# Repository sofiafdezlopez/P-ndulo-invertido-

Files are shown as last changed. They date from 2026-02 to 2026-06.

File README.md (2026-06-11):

# Péndulo invertido

Somos dos alumnos del Grado de Robótica de la Universidad de Santiago de Compostela. En la asignatura de teoria de control se nos ha designado el trabajo de elaborar un robot "péndulo invertido".
El objetivo de este proyecto es que durante la duración de la materia realizaremos la construcción de robot y su control, que se basa en que el robot sea capaz de estabilizarse y mantenerse en una posición vertical.

Para ello hemos organizado todo nuestro trabajo de la siguiente manera:
- `Mecanica/`: Donde se encuentra toda la información sobre la parte mecánica de nuestro robot.
- `Electronica/`: Donde se encuentra toda la información sobre la parte electrica del robot.
- `Software/`: Donde se encuentra toda la información sobre la parte de la programación del robot.
- `README.md`: Fichero explicativo de todo el proyecto.
  
## Procedimiento a seguir

1. __Revisión de proyectos relacionados__ : Realizar una investigación de proyectos existentes para identificar robots similares ya implementados y documentados.
  
2. __Establecer objetivos__ : Debemos tener una idea clara de lo que tenemos que hacer.

3. __Configuración del hardware__ : Escoger los componentes necesarios para la elaboración del robot.

4. __Diseño del chasis__ : Diseñar el chasis ideal que cumpla con las especificaciones.

5. __Comprobación del funcionamiento de los componentes__ : Verificar el funcionamiento de todo el hardware antes del realizar el montaje.

6. __Montaje__ : Orden de montaje del robot.

7. __Implementación del software__ :

8. __Ajuste del PID__ :

## Revisión de proyectos relacionados

En cuanto a la busqueda de proyectos similares hemos encontrado videos donde te muestran el proceso de como construir y programar un robot autobalanceado pero en ningun momento lo documentan de manera que puedas hacerlo sin ver el video.

## Objetivos

- Elegir y adquirir componentes electromecánicos y electronicos.
- Diseñar e imprimir/fabricar el sistema mecánico del péndulo invertido mediante impresión 3D.
- Diseñar e implementar el controlador del péndulo invertido. Diseño de PCB, fabricación y
soldadura de componentes.
- Realizar la implementación del software de control en el microcontrolador ESP32.
- Sintonizar y ajustar el control PID para el péndulo invertido.
- Cumplir las especificaciones.

### Especificaciones

- El sistema debe ser capaz de __mantenerse en posición vertical__ con una tolerancia de ±5
- El sistema debe __compensar los empujones externos__ y volver a la posición vertical.
- El sistema debe ser capaz de poder __iniciar su funcionamiento desde cualquier posición__.

## Configuración del Hardware

Dado que el propósito principal del robot es medir el ángulo de inclinación respecto al suelo, la configuración de sus componentes es sencilla. Los elementos necesarios son los siguientes:

- ESP32
- 2 motores DC 
- 1 driver dual TB6612FNG
- Sensor MPU6050
- Bateria/pila 9V

## Diseño del chasis

A lo largo del proyecto, desarrollamos tres diseños del chasis, optimizandolo basándonos en los resultados de las pruebas:

- **Modelo 1 (Prototipo Inicial)**: Diseño sencillo de una sola planta con la PCB en la parte superior y la batería en la inferior. No resultó práctico ni eficiente, ya que no se tuvó en cuenta un espacio para el interruptor de encendido y este quedó colgando.

- **Modelo 2 (Estructura de Doble Planta)**: Rediseñamos el chasis para solucionar la falta de espacio del primer modelo. Elevamos la PCB para ubicar la batería justo debajo e incluimos una pequeña estructura para fijar el interruptor. Sin embargo, durante las pruebas, observamos que el robot funcionaba de manera más estable y eficiente a una menor altura respecto al suelo.

- **Modelo 3 (Diseño Final)**: Se mantiene la estructura del segundo modelo, pero introduce diferentes alturas en los enganches de los motores. Al elevar la posición de los motores, logramos bajar el cuerpo del robot, optimizando su centro de gravedad y mejorando su funcionamiento.

## Comprobación del funcionamiento de los componentes
Antes de realizar las pruebas de movimiento completo, es fundamental verificar de forma aislada que cada componente electrónico funciona correctamente. Seguimos esta guía de pruebas:

- **1. Test de Alimentación e InterruptorAcción**: Coloca la batería cargada y acciona el interruptor.

   - **Verificación**: Utiliza un polímetro (multímetro) para comprobar que el voltaje en los puntos clave de la PCB sea el correcto y confirma que el LED de estado del microcontrolador se enciende. Si el LED no se ilumina o detectas anomalías en el voltaje, desconecta la alimentación de inmediato para revisar el circuito en busca de cortocircuitos o polaridades invertidas antes de dañar los componentes.
     
- **2. Calibración y Lectura del Sensor de ÁnguloAcción**: Conecta el robot al ordenador mediante el cable USB y carga un script básico de prueba para el sensor.

   - **Verificación**: Abre el serial monitor. Al mover el robot hacia adelante y hacia atrás, los valores del ángulo respecto al suelo deben variar de forma coherente.
     
- **3. Test de Giro de los MotoresAcción**: Eleva el robot (para que las ruedas no toquen el suelo) y ejecuta un código de prueba que haga girar los motores hacia adelante durante 2 segundos y hacia atrás otros 2 segundos.

   - **Verificación**: Asegúrate de que ambas ruedas giran en el sentido correcto. Si una rueda gira al revés, invierte la polaridad de sus cables en la PCB.
  
## Montaje

**Requisito previo**: La pieza o piezas que componen el chasis deben estar completamente impresas.Para este proyecto, la estructura se imprimió con una BAMBU LAB P1S de la universidad bajo las siguientes especificaciones:

- Material: PLA

- Configuración: Parámetros predeterminados por la universidad.

- Tiempo estimado de impresión: 2 horas y 20 minutos aprox.

Una vez retiradas las piezas de la base de impresión y limpios los soportes, se puede realizar el montaje.

**1. Materiales y Herramientas Necesarias**

Tornillos y tuercas: Especificadas en el apartado de mecánica.

Herramientas: Se necesita soldador de estaño, destornillador de estrella y bridas.

**2. Guía de Ensamblaje Paso a Paso**

Paso 1 -> El sistema de tracción: Se fijan los motores al chasis a la altura deseada.

Paso 2 -> Planta Inferior (Alimentación): Se coloca la pila/bateria en su enganche, implementado en el diseño del chasis.

Paso 3 -> Planta Superior (PCB): Se atornilla la PCB, en nuestro caso la enganchamos con bridas debido a que los agujeros de esta son muy pequeños, y se encaja el interruptor.

## Implementación del Software
El software del robot está desarrollado en C++ sobre Arduino. Se organiza en tres capas: utilidades de test y calibración, una biblioteca de control PID propia, y el programa principal de autobalanceo.

El núcleo del sistema es la biblioteca PIDControl, desarrollada para este proyecto. Encapsula tres variantes de controlador PID que pueden seleccionarse en tiempo de ejecución mediante comandos por puerto serie:

**MODE_STANDARD** – PID clásico posicional con acumulador integral y derivada por diferencias finitas.

**MODE_DISCRETE**– Forma recurrente discreta que opera directamente sobre los tres últimos errores mediante coeficientes A0/A1/A2.

**MODE_FILTERED** – PI incremental combinado con derivada filtrada por transformada bilineal, que atenúa el ruido de alta frecuencia en la señal de error.

La estimación del ángulo de inclinación se obtiene del sensor MPU6050 (acelerómetro + giroscopio) mediante un filtro complementario (α = 0,98), que combina la integración del giroscopio a corto plazo con la referencia del acelerómetro a largo plazo.

Los motores se controlan a través de un driver TB6612FNG, con PWM limitado a 170 cuentas para respetar el voltaje nominal de 6 V con la batería de 9 V. El sistema detecta una caída si el ángulo supera ±24° y detiene los motores automáticamente.

Para más detalles sobre la arquitectura, los algoritmos y la guía de uso, ver `Software/README.md/`.

## Ajuste del PID
El ajuste se realizó de forma manual sobre el robot físico, siguiendo este orden:

- Con Ki=0 y Kd=0, se sube Kp hasta que el robot resiste la caída sin oscilar de forma incontrolable.

- Se incrementa Kd hasta amortiguar las oscilaciones y conseguir un comportamiento casi estable.

- Con Kp y Kd fijados, se añade un Ki pequeño para eliminar el error estacionario. Un valor excesivo desestabiliza el sistema.

- El ángulo de equilibrio real del robot se midió en aproximadamente 6° (el signo depende de la orientación del MPU6050). Los valores que produjeron un balanceo estable fueron:

| Kp | Ki | Kd | dt |
| :---: | :---: | :---: | :---: |
| `17` | `0` | `1.2` | `10 ms` |

De los tres modos probados, MODE_FILTERED mostró la respuesta más suave, ya que el filtro paso-bajo en la derivada reduce el efecto del ruido del MPU6050 sobre los motores.

## Multimedia

<details>
  <summary>Haz clic aquí para ver las fotos y videos</summary>
  
  ### Fotos del modelo
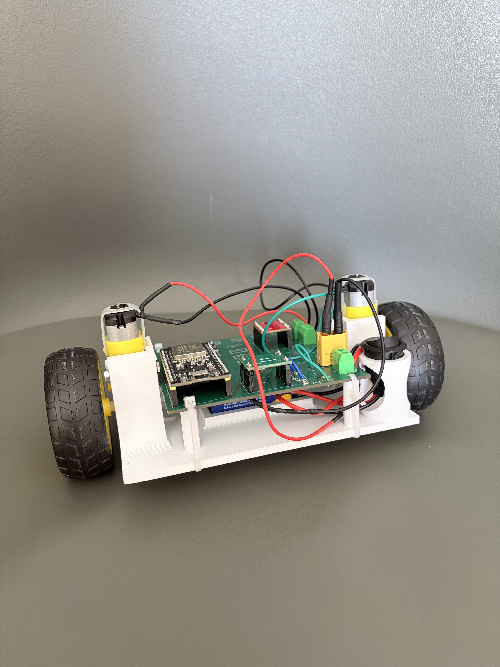
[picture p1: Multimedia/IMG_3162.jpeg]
Vista frontal
  
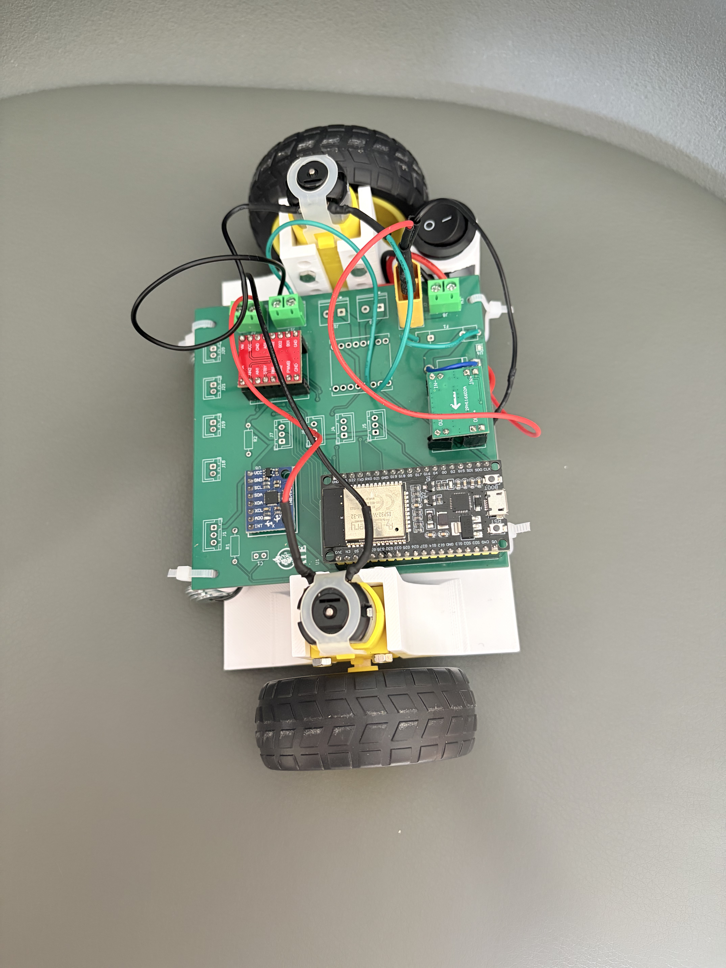
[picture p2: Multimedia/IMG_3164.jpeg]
Vista de planta
  
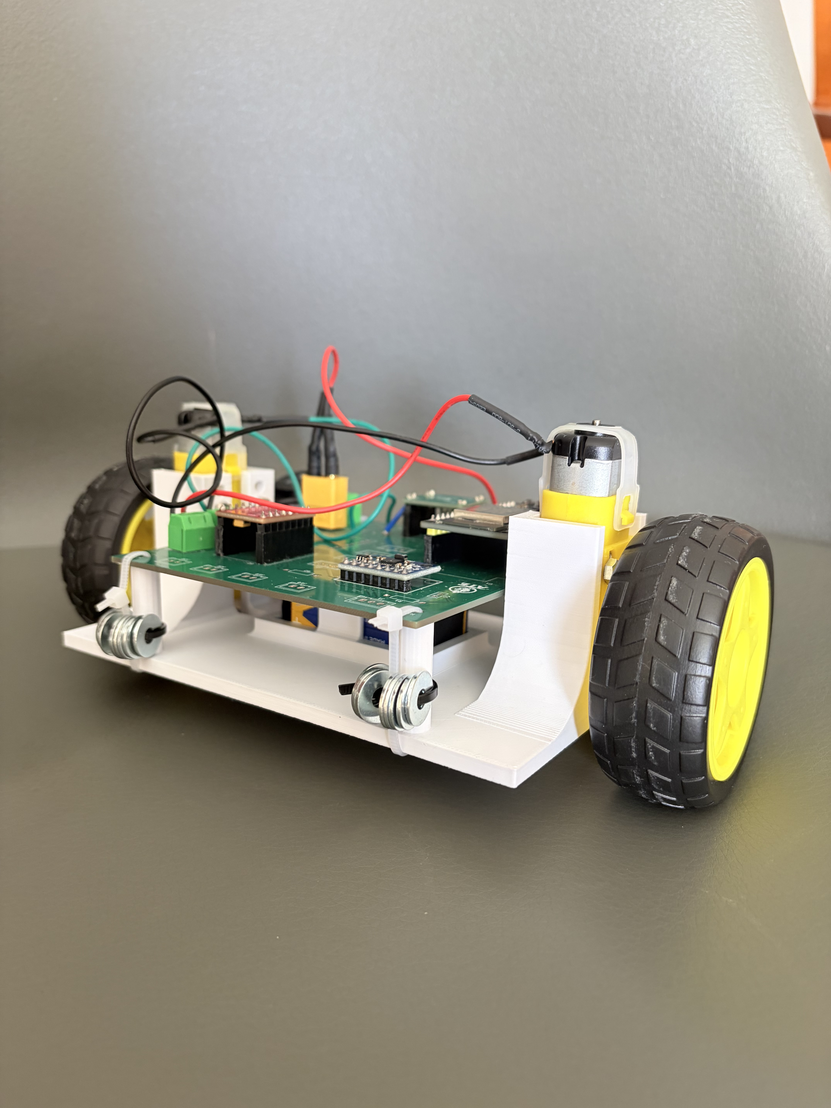
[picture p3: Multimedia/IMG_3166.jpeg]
Vista posterior
  
  
  ### Videos de demostración
  [Mira el video 1 aquí](Multimedia/video1.mov) 
  
  [Mira el video 2 aquí](Multimedia/video2.mov) 
  
  [Mira el video 3 aquí](Multimedia/video3.mov) 
</details>

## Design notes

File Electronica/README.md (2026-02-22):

# Diseño Electrónico del Robot
En esta carpeta se incluyen los diseños y materiales electrónicos necesarios para la construcción de un robot autobalanceado.

La estructura de la carpeta es la siguiente:

- `README.md/`: Este fichero.
- `PCB.zip/`: Carpeta comprimida del modelado de la PCB en Kicad.
- `Componente.md/`: Fichero que contiene la lista de componentes electrónicos.

## Objetivo del Diseño
Placa compacta que aloja:
- Un **ESP32** como MCU/Wi-Fi/Bluetooth.
- Control de **4 motores DC** (2 drivers duales TB6612FNG).
- Lectura de sensores IR y MPU6050.
- Gestión de **alimentación** desde LiPo.
- Conectores para batería, motores, sensores y programación.

## Especificaciones PCB
- **Dimensiones:** ~ 10 × 10 cm 
- **Capas:** 2.

## Adaptaciones de la PCB
La PCB original fue diseñada para su uso en un robot de tipo sumo. Sin embargo, en este proyecto no se utilizarán algunos de los elementos incluidos en el diseño, como por ejemplo los conectores para sensores infrarrojos y finales de carrera, ya que no son necesarios para el funcionamiento del sistema implementado.

Por este motivo, antes del montaje se procederá a eliminar las secciones de la PCB que no serán utilizadas, recortando las partes innecesarias y dejando únicamente la zona correspondiente a los componentes funcionales del proyecto. Esta modificación permite simplificar la estructura del hardware y reducir el tamaño final del módulo electrónico.

## Esquema funcional
- **Entrada batería** → protección (diodo) → **regulador a 5V** → 5V 
- 5V  → ESP32 → **regulador a 3.3V** → 3.3V
- 3.3V: pines GPIO → drivers / sensores / I²C
- **Driver motores (TB6612)**: alimentado a 12V (Vm), señales IN1/IN2 desde ESP32, pin PWM para velocidad.
- Sensores: Conectados a GPIOs del ESP32.

## Protección y seguridad
- Fusible rearmable (PTC) en la entrada de la batería.
- Diodo de protección contra conexión inversa (schottky).
- Indicador LED de encendido (5V) y LED de estado ESP32.

## Prueba de la resistencia de protección en TX0

El uso del GPIO correspondiente a TX0 puede ocasionar problemas. Para mitigar el riesgo de quemar el pin GPIO y las interrupciones en la comunicación serial, así como para facilitar el debug y los tests de forma cómoda y segura, aplicamos las siguientes medidas:

- Colocar una **resistencia en serie** de 4,7KΩ entre el Pin y el Bumper (protección ante el cortocircuito).
- Usa el GPIO TX0 para un bumper (mitigar entradas).

### Procedimiento de prueba

Realiza este procedimiento con el robot APAGADO y desconectado.

1. Pon el multímetro en modo Resistencia (Ω).
2. Coloca una punta en el pin GPIO 1 del ESP32 (o en la soldadura correspondiente).
3. Coloca la otra punta en GND (cualquier punto de masa).
4. **Presiona el Bumper**.
5. **Verifica la lectura:** Debes ver el valor aproximado de tu resistencia (**4.7 kΩ**).

- Si ves **0 Ω** (o muy cerca de cero): La resistencia no está en serie, hay un cortocircuito directo. **No lo enciendas hasta solucionarlo**.
- Si OL (Over Limit): El interruptor no está cerrando el circuito.

### ¿Por qué funciona esto?

Esta configuración es segura y funcional por dos razones matemáticas:

1. **Seguridad (Protección del Pin):**
Si el pin TX0 intenta enviar datos (3.3V) mientras pulsas el botón, la resistencia limita la corriente máxima, evitando quemar el transistor interno del ESP32.

$$I_{max} = \frac{3.3V}{4700\Omega} \approx 0.7 mA$$

*(El ESP32 soporta hasta 12mA, por lo que 0.7mA es totalmente seguro).*

2. **Funcionalidad (Lectura correcta):**
Al leer el botón, el ESP32 activa una resistencia interna de pull-up (~45kΩ). Al pulsar, se crea un divisor de tensión:

$$V_{pin} = 3.3V \times \frac{4.7k\Omega}{4.7k\Omega + 45k\Omega} \approx 0.31V$$

*(0.31V es interpretado como un "LOW" lógico por el ESP32, por lo que detecta la pulsación correctamente).*

Entoces:

- Sin presionar: El pin está en HIGH (3.3V) gracias al pull-up interno. digitalRead devuelve 1.
- Presionado: El pin baja a 0.31V (LOW). digitalRead devuelve 0.

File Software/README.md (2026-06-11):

## Diseño del Software del Robot

En esta carpeta se incluye la implementación del diseño del software necesario para el autobalanceado del robot.

La estructura de la carpeta es la siguiente:
- `README.md/`: Este fichero.

La estructura de este fichero es la siguiente:

1. [Estructura](#estructura)
2. [Diagrama de bloques](#diagrama-de-bloques)
3. [Compilación](#compilación)
4. [Arquitectura](#arquitectura)

## Estructura
``` none
Software/
├── lib/
│   └── PIDControl/              ← Biblioteca de control PID propia
│       ├── src/
│       │   ├── PIDControl.h     ← Declaración de la clase y enumeración PIDMode
│       │   └── ControlPID.cpp   ← Implementación de los tres modos
│       ├── library.properties   ← Metadatos para el IDE de Arduino
│       └── KEYWORDS.txt         ← Coloreado de sintaxis
├── src/
│   ├── main/
│   │   └── main.ino             ← Programa inicial
│   └── main_lib_pid/
│       └── main_lib_pid.ino     ← Programa principal con los tres modos PID
└── test/
    ├── calibracion_mpu6050/
    │   └── calibracion_mpu6050.ino  ← Utilidad de calibración del IMU
    ├── motores/
    │   └── motores.ino              ← Test de giro y dirección de motores
    └── mpu6050/
        └── mpu6050.ino              ← Test de lectura raw del sensor
```

## Diagrama de bloques
``` none
┌─────────────────────────────────────────────────────────┐
│                        ESP32                            │
│                                                         │
│  ┌──────────┐    ┌──────────────┐    ┌───────────────┐  │
│  │ MPU6050  │───▶│   Filtro     │───▶│  Controlador │  │
│  │ IMU I²C  │    │complementario│    │  PID (modo    │  │
│  └──────────┘    └──────────────┘    │  seleccionado)│  │
│                       α=0,98         └──────┬────────┘  │
│                                             │           │
│  ┌──────────────────────────┐               ▼           │
│  │   Serial (115200 baud)   │    ┌──────────────────┐   │
│  │  S → MODE_STANDARD       │    │  Driver TB6612   │   │
│  │  D → MODE_DISCRETE       │    │  Motor A  Motor B│   │
│  │  F → MODE_FILTERED       │    └──────────────────┘   │
│  └──────────────────────────┘                           │
└─────────────────────────────────────────────────────────┘
```

## Compilación

Instalar la biblioteca PIDControl: en el Arduino IDE, Sketch → Include Library → Add .ZIP Library... y seleccionar la carpeta `lib/PIDControl/`.

1- Abrir `src/main_lib_pid/main_lib_pid.ino`.

2- Seleccionar la placa ESP32 Dev Module y el puerto correspondiente.

3- Compilar y subir.

4- Abrir el Monitor Serie a 115200 baud para ver telemetría y enviar comandos.

Para calibrar el MPU6050 (solo necesario si se cambia el sensor o el montaje): abrir y ejecutar `test/calibracion_mpu6050/calibracion_mpu6050.ino` y copiar los offsets resultantes en el sketch principal.

## Arquitectura

**Estimación del ángulo — Filtro complementario**

- El ángulo de inclinación se estima fusionando dos fuentes del MPU6050:
    
   * Acelerómetro: proporciona el ángulo absoluto mediante atan2, pero es ruidoso ante vibraciones.
   * Giroscopio: integra la velocidad angular para obtener el ángulo incremental; preciso a corto plazo pero deriva con el tiempo.
    
- El filtro complementario combina ambas fuentes:
```none
ang_y = α · (ang_y_prev + gy_dps · dt) + (1 − α) · accel_ang
```
&nbsp;&nbsp;&nbsp;&nbsp;&nbsp;&nbsp;Con α = 0,98: el 98 % del peso recae en el giroscopio (respuesta rápida) y el 2 % en el acelerómetro (corrección de deriva).

**Biblioteca PIDControl — Tres modos de control**

- La clase PIDControl implementa tres variantes del controlador PID discreto:

&nbsp;&nbsp;&nbsp;&nbsp;&nbsp;&nbsp;`MODE_STANDARD — PID clásico posicional`

&nbsp;&nbsp;&nbsp;&nbsp;&nbsp;&nbsp;&nbsp;Calcula la salida acumulando la integral del error y la derivada por diferencias finitas:
```none
u(k) = Kp·e(k) + Ki·Σe·dt + Kd·(e(k) − e(k−1))/dt
```
<br>

&nbsp;&nbsp;&nbsp;&nbsp;&nbsp;&nbsp;`MODE_DISCRETE — Forma recurrente directa`

&nbsp;&nbsp;&nbsp;&nbsp;&nbsp;&nbsp;&nbsp;Expresa la salida directamente en función de los tres últimos errores, sin estado acumulado:
```none
u(k) = A0·e(k) + A1·e(k−1) + A2·e(k−2)
```
&nbsp;&nbsp;&nbsp;&nbsp;&nbsp;&nbsp;&nbsp;donde 
```none
A0 = Kp + Ki·dt + Kd/dt, A1 = −Kp − 2·Kd/dt, A2 = Kd/dt.
```

&nbsp;&nbsp;&nbsp;&nbsp;&nbsp;&nbsp;`MODE_FILTERED — PI incremental con derivada filtrada`

&nbsp;&nbsp;&nbsp;&nbsp;&nbsp;&nbsp;&nbsp;Suma incrementalmente la parte PI y aplica un filtro paso-bajo bilineal sobre la parte derivativa para atenuar el ruido:
```none
Δu_PI(k) = (Kp + Ki·dt)·e(k) − Kp·e(k−1)
d(k)      = A0d·e(k) + A1d·e(k−1) + A2d·e(k−2)
fd(k)     = α1·(d(k) + d(k−1)) − α2·fd(k−1)    ← filtro bilineal
u(k)      = u(k−1) + Δu_PI(k) + fd(k)
```
&nbsp;&nbsp;&nbsp;&nbsp;&nbsp;&nbsp;&nbsp;La constante de tiempo del filtro es τ = Kd/(Kp·N), con N = 5 por defecto.

**Control de motores**

- La salida del controlador PID se aplica a ambos motores en sentido opuesto (el robot avanza para compensar la inclinación). La función moveMotor gestiona la dirección mediante los pines IN1/IN2 del driver y la velocidad mediante PWM:

    * Salida positiva → motor A avanza, motor B retrocede.
    * Salida negativa → motor A retrocede, motor B avanza.

- PWM limitado a 170 cuentas (≈ 6,7 V efectivos sobre 9 V de batería).

**Protección por caída**

- Si el ángulo de inclinación supera ±24°, el sistema detiene los motores, reinicia todos los controladores PID y espera a que el robot sea recolocado manualmente. Esto evita que los motores fuercen contra el suelo y protege el hardware.

**Cambio de modo en tiempo de ejecución**

- Enviando S, D o F por el Monitor Serie se cambia el controlador activo sin necesidad de reiniciar el robot ni recompilar. Al cambiar de modo se reinician todos los controladores para evitar transitorios causados por valores residuales en los buffers de error.

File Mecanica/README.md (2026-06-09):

# Diseño Mecánico del Robot
En esta carpeta se incluyen los diseños y materiales mecánicos necesarios para la construcción de un robot autobalanceado.

La estructura de la carpeta es la siguiente:

- `README.md/`: Este fichero.
- `CHASIS.ipt/`: Modelado 3D del chasis en Inventor.
- `CHASIS_V2.stl/`: Archivo .stl del chasis en Inventor.
- `CHASIS_V2.gcode/`: Archivo .gcode del chasis en Inventor.
- `Componentes_mecanicos.md/`: Fichero que contiene la lista de componentes mecánicos.

## Estructura General
- **Dos ruedas motrices** (una de lado izquierdo y otra del lado derecho) con dos motores DC y reducturas, colocados respectivamente.
- **Chasis plano de dos plantas**:
    - **Inferior**: Bateria y motores.
    - **Superior**: Electrónica y sensor.

 ## Dimensiones Orientativas
- **Largo***~ 15 cm
- **Ancho**~ 10 cm
- **Altura**~ 3 cm
- **Distancia entre Ruedas**~ 15 cm
  
 ## Material Utilizado 
 - **Chasis**: PLA/PETG (Impresión 3D)
 - **Motores:** mini micromotores DC con engranajes de rueda dentada.
 - **Ruedas:** diámetro 6–7 cm, goma antideslizante (Mecanum).
 - **Batería:** Varta (9 V).
 - **Cables**
   
## Esquema simple (vista superior)
<pre>
┌─────────────────────────────────────────┐
│        Placa controladora arriba        │
│                                         │ 
[Rueda L]Motor               Motor[Rueda R]
│                                         │ 
│        Batería en el centro             │
└─────────────────────────────────────────┘
</pre>

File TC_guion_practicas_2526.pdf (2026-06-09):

Teoría de Control

Grado de Robótica

2025 - 2026

## GUIÓN DE PRÁCTICAS

## Índice general

1. Modelado de sistemas electromecánicos | 3
2. PID en tiempo contínuo | 7
3. Compensación Proporcional-Integral-Derivativa | 12
4. PID en tiempo discreto | 14
5. Modelado de sistemas en el espacio de estados | 17
EPSE - Campus Terra (Lugo) | 1 / 63 | e.comesana@usc.es

6. Proyecto péndulo invertido | 22
A. Ejemplo de informe del proyecto péndulo invertido | 24
B. Manual de robot Kobuki/Turtlebot2 | 39
EPSE - Campus Terra (Lugo) | 2 / 63 | e.comesana@usc.es

## Práctica 1. Modelado de sistemas electromecánicos

## 1.1. Resumen repaso de Fundamentos de Automática

A continuación se repasan varios conceptos básicos sobre el uso de Matlab y Simulink ya vistos en la asignatura de Fundamentos de Automática

### 1.1.1. Definición de funciones de transferencia

En Matlab las funciones de transferencia se pueden definir de varias formas. Por ejemplo para la función de transferencia

G(s) = Y (s)
X(s)

=

5s − 3
3s

2 + 5s − 7
1. Mediante cociente de polinomios:

% Comentario
num = [5 -3];
den = [3 5 -7];
2. En función de sus ceros (z), polos (p) y ganancia (g):

z = [5 -2];
p = [2+i 2-i -5];
k = 10;
G = zpk(z,p,k);
3. Mediante el uso de variables simbólicas:

s = tf('s') % s es un objeto transfer function. G = 5*s/(3*s^2 + 7);

Notas de interés:

En https://es.mathworks.com/help/control/ref/tf.html está disponible la documentación de la función tf. (https://es.mathworks.com/help/control/ref/tf.html)

El comando tfdata (https://es.mathworks.com/help/ident/ref/dynamicsystem.tfdata.html) permite obtener el numerador y el denominador de una ft.

El comando zpkdata (https://es.mathworks.com/help/ident/ref/dynamicsystem.zpkdata.html) permite obtener los ceros, polos y ganancia de una ft.

Otras funciones para la extracción de información de un ft se pueden consultar en https: //es.mathworks.com/help/ident/data-extraction.html

El comando residue (https://es.mathworks.com/help/matlab/ref/residue.html) permite calcular la descomposición en fracciones simples de una ft.

### 1.1.2. Interconexión y operaciones con bloques

Las funciones feedback, (https://es.mathworks.com/help/control/ref/lti.feedback.html) series (https://es.mathworks.com/help/control/ref/lti.series.html) y parallel (https://es.mathworks.com/help/control/ref/lti.parallel.html) permiten realizar realizar conexiones entre bloques para su reducción:

EPSE - Campus Terra (Lugo) | 3 / 63 | e.comesana@usc.es

K = tf(10, 1);
G = tf(3, [1 1]);
H = tf(4, [1 5 0]);
fb_1 = feedback(G,H,-1);
olp_1 = series(K, fb_1);
C = feedback(olp_1 , 1, -1);

Más información sobre este tipo de funciones en: https://es.mathworks.com/help/control/model-interconnection.html?s_tid=CRUX_lftnav (https://es.mathworks.com/help/control/model-interconnection.html?s_tid=CRUX_lftnav)

### 1.1.3. Visualización de la respuesta de un sistema

La función step (https://es.mathworks.com/help/ident/ref/dynamicsystem.step.html) permite analizar la respuesta de un sistema
ante un escalón unitario. La función plot (https://es.mathworks.com/help/matlab/ref/plot.html) permite obtener la representación gráfica de la respuesta

G = tf([1 10], [2 3 10]);
t_sim = 10; # Tiempo de simulacion.
[y t] = step(G, t_sim);
plot(x, y);
grid;
title('Respuesta␣a␣entrada␣escalon␣de␣G'); xlabel('t(s)');
ylabel('y(t)');

Más información relativa a herramientas análisis de repuesta y
visualización en https://es.mathworks.com/help/ident/response-visualization.html

### 1.1.4. Modelado de sistemas con Simulink

Mediante Simulink podemos crear diagramas de bloques de forma gráfica. Para ejecutarlo:

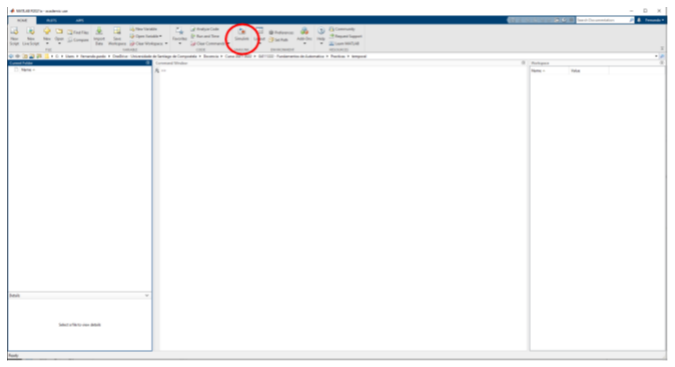
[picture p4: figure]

EPSE - Campus Terra (Lugo) | 4 / 63 | e.comesana@usc.es

Y seleccionar “Create Blank Model”:

Se abrirá el área de trabajo donde construir el modelo de un sistema:

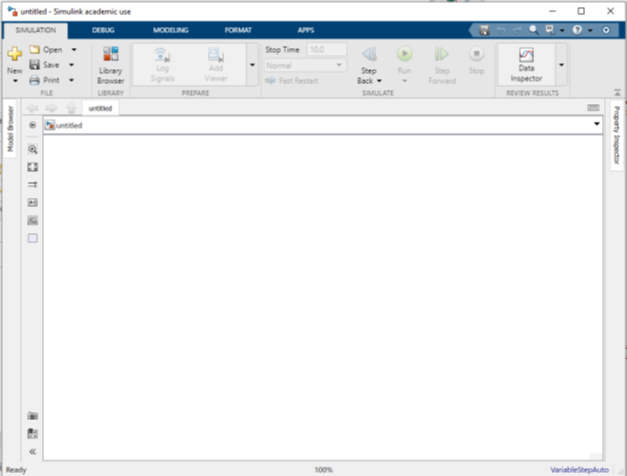
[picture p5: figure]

Para acceder a la librería de componentes pulsar “Library Browser”:

Usaremos las categorías:

Continuous: Análisis de sistemas continuos

Discrete: Análisis de sistemas discretos

Sources: Bloques de generación de señales

EPSE - Campus Terra (Lugo) | 5 / 63 | e.comesana@usc.es

Sinks: Herramientas de visualización

Math operation: Operaciones matemáticas básicas

## 1.2. Ejercicios a realizar

1. Para el sistema de la figura obtener la función de transferencia del sistema X(s)/F(s) y, usando Matlab:
a) Simular la respuesta del sistema ante una entrada escalón.
b) Obtener la respuesta del sistema ante una entrada impulso.
c) Obtener los ceros, polos y ganancia del sistema.
d) Analizar el comportamiento del sistema cuando cambian los valores de las constantes del sistema (m, k y b)
Datos iniciales: m = 2 kg, b = 10 N s m−1

, k = 20 N m−1

2. Para el sistema del problema 1.13 (masa en rotación con acoplamiento elástico), usando Matlab:
a) Simular la respuesta del sistema ante una entrada escalón.
b) Obtener la respuesta del sistema ante una entrada impulso.
c) Obtener los ceros, polos y ganancia del sistema.
d) Analizar el comportamiento del sistema cuando cambian los valores de las constantes del sistema (m, k y b).
3. Construye en Simulink el diagrama de bloques correspondiente al problema 1.9 (suspensión de un coche). Usando los valores disponibles en los apuntes de teoría para este sistema, obtener la respuesta del sistema ante una entrada escalón y una entrada impulso.
4. Construye en Simulink el diagrama de bloques correspondiente al sistema del problema 1.16 (motor con reductora) y obtener la respuesta de sistema ante una entrada escalón. Seleccionar valores para las constantes del sistema y observar el efecto en la respuesta de su cambio.
5. Construye con Simulink el diagrama de bloques del problema 1.19 y responder a las preguntas del problema.
EPSE - Campus Terra (Lugo) | 6 / 63 | e.comesana@usc.es

## Práctica 2. PID en tiempo contínuo

Vamos a trabajar con un sistema realimentado,
el sistema usa la señal de entrada (señal de referencia, r) y la señal de salida (señal manipulada,
y) para generar una señal de error (e) a partir de la cual, por acción del sistema de control (C(s)), generaremos una señal de control (u) para ac-tuar sobre el sistema (F(s)) y llevar la salida del
sistema al valor buscado.

Si recordamos la expresión matemática del PID, el controlador que vamos a usar en esta práctica:

u(t) = Kpe(t) + Ki

∫
e(t)dt + Kd

de(t)
dt

Y en el espacio de Laplace:

U(s) = Kp +

Ki
s

+ Kps

Vemos que para configurar (sintonizar) un controlador PID debemos establecer el valor de tres constantes Kp, Ki y Kd.

## 2.1. PID con Matlab

Para definir un controlador PID en Matlab, podemos construirlo

a partir de su función de transferencia:

Kp = 1;
Ki = 1;
Kd = 1;

s = tf('s');
C = Kp + Ki/s + Kd*s;

o usando la función pid: (https://es.mathworks.com/help/control/ref/pid.html)

Kp = 1;
Ki = 1;
Kd = 1;

C = pdi(Kp, Ki, Kd);
tf(C) % Para mostrar la ft

## 2.2. Ejercicio: Control PID de la fuerza aplicada sobre una masa

Dado el sistema masa-resorte-amortiguador de la figura, la ecuación diferencial que modela el sistema tiene la forma:

m

d

2x
dt²

+ b

dx
dt + kx = F

Que en el dominio de Laplace:

EPSE - Campus Terra (Lugo) | 7 / 63 | e.comesana@usc.es

ms²X(s) + bsX(s) + kX(s) = F(s)

Es decir, que la función de transferencia del sistema es:

X(s)
F(s)

=

1
ms² + bs + k

Si los parámetros del sistema son m = 1 kg, b = 10 N s m−1

, k = 20 N m−1 y la fuerza aplicada es de F = 1 N.

Entonces usando Matlab podemos obtener en primer lugar la respuesta en lazo abierto del sistema con:

s = tf('s');
P = 1/(s^2 + 10*s + 20);
step(P)

Para obtener la respuesta, por ejemplo, a la acción de un controlador proporcional, podemos hacer:

Kp = 300;
C = pid(Kp);
T = feedback(C*P, 1);
t = 0:0.01:2; % Permite definir eje de tiempos con mayor resolucion step(T,t)

### 2.2.1. Cuestiones a resolver

Dado el planteamiento anterior para el sistema mostrado, reponder a las siguientes preguntas:

1. Obtener la respuesta en lazo abierto del sistema ante una entrada escalón unitario. Graficar la entrada y la salida del sistema. ¿De que naturaleza son las magnitudes y cuales son sus unidades de las variables en la gráfica presentada?
2. Testear la respuesta del sistema cuando se emplea un controlador P, PD, PI y PID ¿Qué diferencias se observan entre las respuestas del sistema para cada uno de los controladores? Escoger valores arbitrarios para sintonizar el PID y ajustarlos para entender el efecto que cada termino del PID.
3. Sintonizar un controlador PID de forma manual, intentando obtener el menor tiempo de subida posible sin que se produzca sobreoscilación o sobrepasamiento. El tiempo de subida ha de ser inferior a 0, 1.
4. Desarrollar en Matlab un script que obtenga de forma automática los parámetros de controladores P, PI y PID, empleando el método de Ziegler-Nichols de lazo abierto, descrito en la teoría.
5. Comparar la respuesta entre el sistema controlador por el PID sintonizado manualmente y el sintonizado mediante Ziegler-Nichols
EPSE - Campus Terra (Lugo) | 8 / 63 | e.comesana@usc.es

## 2.3. Sintonizado de PID automático (Autotune)

Matlab ofrece una herramienta automática para escoger el PID accesible a través del comando pid-Tuner. (https://es.mathworks.com/help/control/ref/pidtuner.html) Para obtener el controlador proporcional óptimo (según este autotuner) para el proceso P anteriormente definido

pidTuner(P,'p');

Hacer click en ”Show Parameters”para ver los valores de sintonización del controlador.

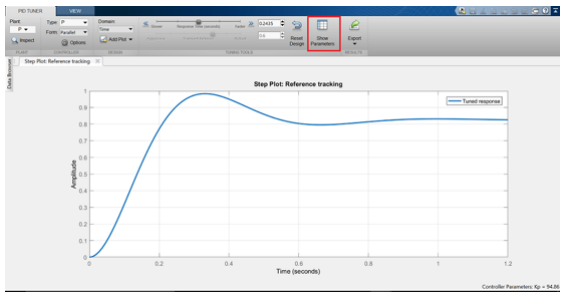
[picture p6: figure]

También podemos realizar la comparación entre un PID base y un PID optimizado, pasando como segundo parámetro a la función pidTuner (https://es.mathworks.com/help/control/ref/pidtuner.html) la función de transferencia de otro PID (baseline).

pidTuner(P,'p');

De nuevo, haciendo clic en ”Show Parameters”se pueden comparar las constantes y características dinámicas del sistema controlado por un PID sintonizado automáticamente y otro previo (baseline).

Por último, mediante los controles disponibles en la herramienta (indicados en la figura anterior), se pueden ajustar los parámetros dinámicos para ajustar la respuesta del sistema.

### 2.3.1. Cuestiones

1. Obtener las respuestas del sistema cuando está controlado con un controlador P, PD, PI y PID sintonizados automáticamente con pidTuner. (https://es.mathworks.com/help/control/ref/pidtuner.html)
2. Comparar las respuestas obtenidas para cada tipo de controlador, ¿que diferencias se observan?
3. Comparar las respuestas obtenidas con los controladores sintonizados con pidTuner (https://es.mathworks.com/help/control/ref/pidtuner.html) y los sintonizados usando el método de Ziegler Nichols.
EPSE - Campus Terra (Lugo) | 9 / 63 | e.comesana@usc.es

4. Comparar el resultado de la sintonización de automática PID para el sistema inicial (función de transferencia P) con el PID sintonizado manualmente para minimizar el tiempo de subida. Usando los controles de pidTuner (https://es.mathworks.com/help/control/ref/pidtuner.html) para ajustar los parámetros dinámicos para igualar

## 2.4. PID con Simulink

Implementar el sistema (servomotor) de la figura, empleando elementos básicos de Simulink. Suponer unos valores arbitrarios para las constantes del PID.

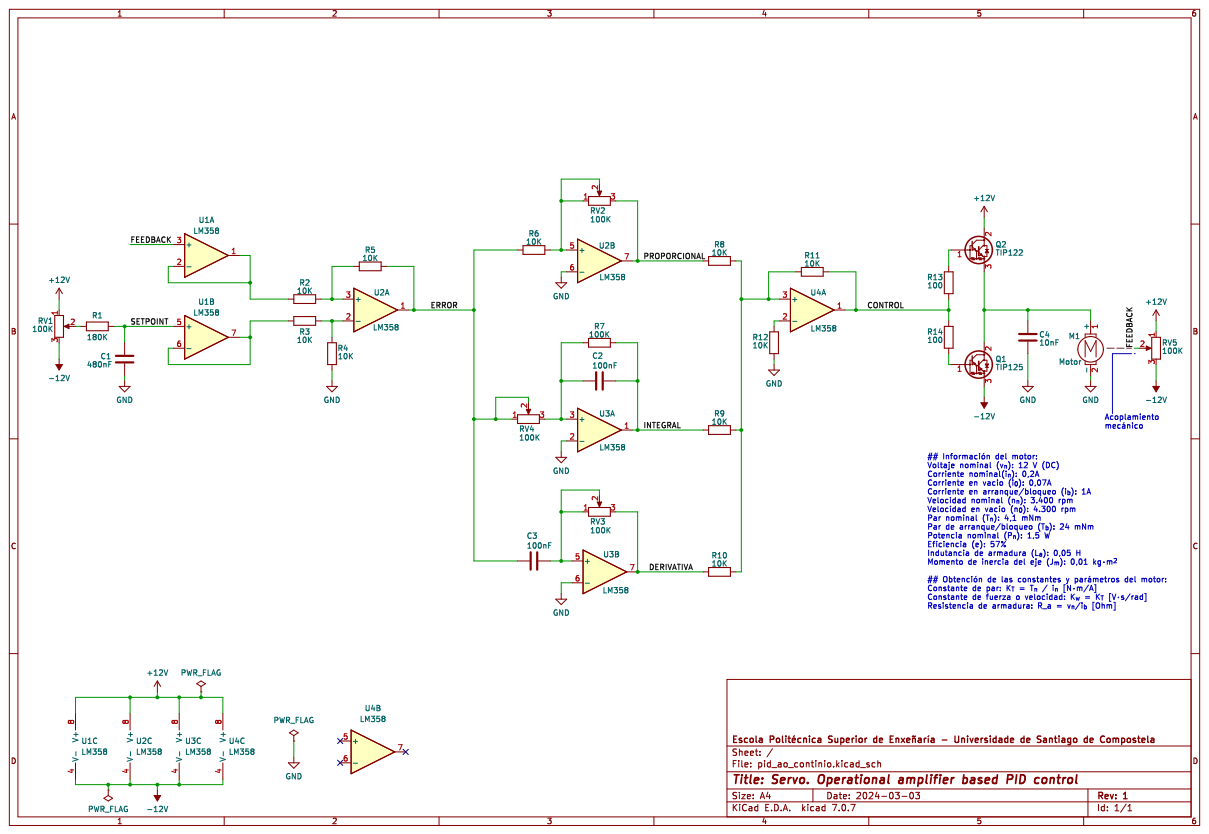
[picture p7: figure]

Sustituir el PID con realizado con amplificadores operacionales con el bloque PID disponible en Simulink

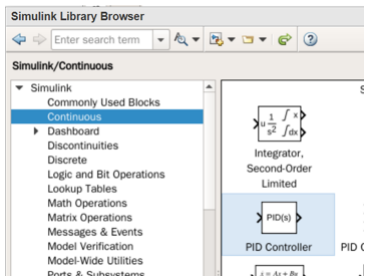
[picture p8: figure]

EPSE - Campus Terra (Lugo) | 10 / 63 | e.comesana@usc.es

El motor empleado tiene las siguientes características:

Parameter | Units | Value | Parameter | Units | Value
Nominal voltaje No-load speed No-load current Rated speed Rated torque Stall torque Starting current | V rpm A rpm mN·m mN·m A | 12 4300 0.07 3400 4.1 24 1.0 | Max power Max efficiency Terminal resistance Terminal inductance Torque constant Speed constant Axis inertia | W % Ω H mN·m/A V·s/rad kg·m² | 1.5 57 12 0.05 20.5 167 0.01

Además tiene acoplado una reductora de relación 48:1 en su eje.

### 2.4.1. Cuestiones

1. Como usarías el método de Ziegler-Nichols para sintonizar las constantes del PID
2. Prueba las herramientas de Autotune de las de dispone el bloque PID de Simulink.
EPSE - Campus Terra (Lugo) | 11 / 63 | e.comesana@usc.es

## Práctica 3. Compensación Proporcional-Integral-Derivativa

La compensación proporcional-integral-derivativa com-bina la acción de la compensación PI y PD:

1. La compensación PD ajusta la respuesta tran-sitoria.
2. La compensación PI mejora el error en estado estacionario.

La función de transferencia de un controlador PID, visto en teoría es:

D(s) = Kp +

Ki
s

+ Kds =

Kds

2 + Kps + Ki
s

Es decir, la función de transferencia del controlador PID tiene dos ceros y un polo en el origen:

La pareja polo/cero cerca del origen se determinan mediante lo visto para el diseño de un compensador PI.

La localización del segundo cero se determina mediante lo visto para el compensador PD.

Procedimiento de diseño de un compensador PID

1. Determinar la posición de los polos dominantes a partir de los requerimientos de diseño para la respuesta en lazo cerrado.
2. Diseñar un compensador PD (posición del cero y ganancia) para colocar el lugar de las raices adecuado y obtener los polos en lazo cerrado buscados.
3. Simular el sistema con el compensador PD e iterar si es necesario para terminar de ajustar la respuesta del sistema.
4. Diseñar el compensador PI y añadirlo al sistema ya compensado con PD, determinar la ganancia necesaria para mantener la localización de los polos dominantes en lazo cerrado buscados.
5. Determinar los parámetros del controlador PID: Kp, Ki y Kd.
6. Simular el sistema PID-compensado e iterar para terminar de ajustar la respuesta.

## 3.1. Ejercicio: Sistema con compensación PID

Diseñar la compensación PID para satisfacer las siguientes especificaciones:

ts = 2s. Considerando un error de 2 %.

%OS = 20 %
Error en estado estacionario cero para una referencia constante.

Para un sistema cuya función de transferencia es:

F(s) = | 15
s

3 + 10s

2 + 27s + 18

EPSE - Campus Terra (Lugo) | 12 / 63 | e.comesana@usc.es

### 3.1.1. Cuestiones

1. Obtener los polos dominantes buscados, en lazo cerrado para las especificaciones listadas anteriormente.
2. Obtener el lugar de las raíces para este sistema en lazo cerrado con un controlador proporcional.
3. Diseñar un compensador PD que satisfaga las condiciones dinámicas:
a) Calcular la contribución angular del cero del compensador PD para que se cumpla el criterio de ángulos.
b) Obtener la posición del cero en el eje real.
c) Obtener el valor de ganancia necesario para conseguir los polos buscado, aplicando el criterio de magnitud.
d) Simular la respuesta del sistema ante una entrada escalón y comparar la respuesta del sistema compensado y sin compensar (con controlador proporcional).
4. Añadir un compensador PI, elegir la posición de su cero y simular e iterar hasta obtener la respuesta buscada.
5. Obtener los valores de las constantes del PID diseñado.
EPSE - Campus Terra (Lugo) | 13 / 63 | e.comesana@usc.es

## Práctica 4. PID en tiempo discreto

El análisis de sistemas de control en tiempo discreto es muy similar al análisis en tiempo continuo. La principal diferencia es que en tiempo discreto, las señales y las funciones de transferencia se representan en el dominio de la frecuencia de la transformada Z en lugar de la transformada de Laplace.

Para realizar el diseño de la implementación de un controlador PID en un microcontrolador (MCU) o una FPGA, se requiere discretizar el controlador PID. La discretización de un controlador PID. Para esto ser realizan aproximaciones para las derivadas de primer orden empleando diferencias finitas.

La señal de salida del controlador y la señal de error se discretizan en el tiempo con un periodo de muestreo ∆t.

## 4.1. Discretización de un controlador PID

La ecuación diferencial de un controlador PID en tiempo continuo es:

u(t) = Kpe(t) + Ki

∫
e(t)dt + Kd

de(t)
dt | (4.1)

y derivando ámbos miembros de la ecuación respecto al tiempo, obtenemos:

du(t)
dt = Kp

de(t)
dt + Kie(t) + Kd

d

2
e(t) dt² | (4.2)

Si la derivada se aproxima como:

f(t)
dt

≈

f(tk) − f(tk−1)
∆t
| (4.3)

siendo k el número de muestra y ∆T el periodo de muestreo.

Entonces la ecuación diferencial del controlador PID se puede aproximar como:

uk − uk−1
∆t

= Kp

ek − ek−1
∆t

+ Kiek + Kd

ek − 2ek−1 + ek−2
∆t

2

(4.4)

que simplificando y agrupando términos tenemos la ecuación para un PID en tiempo discreto:

uk = uk−1 +

(
Kp + Ki∆t +

Kd
∆t

)
ek −

(
Kp +

2Kd
∆t

)
ek−1 +

Kd
∆t
ek−2 | (4.5)

o, en términos de los tiempos de integración y derivación:

uk = uk−1 + Kp

[(1 +
∆t
Ti

+

Td
∆t

)
ek −

(
1 +

2Td
∆t

)
ek−1 +

Td
∆t

ek−2

]
(4.6)

donde Ti = Ki/Kp y Td = Kd/Kp.

EPSE - Campus Terra (Lugo) | 14 / 63 | e.comesana@usc.es

### 4.1.1. Implementación de controlador PID en tiempo discreto

Las ecuaciones anteriores se pueden implementar en un microcontrolador o una FPGA. La implementación mediante un bucle de control que se ejecuta a la frecuencia de muestreo ∆t.

El siguiente pseudocódigo muestra la implementación de un controlador PID en tiempo discreto:

previous_error := 0
integral := 0
start:
error := setpoint - measured_value
integral := integral + error * dt
derivative := (error - previous_error) / dt
output := Kp * error + Ki * integral + Kd * derivative previous_error := error
wait(dt)
goto start

### 4.1.2. PID como un filtro IIR

La transformada Z de un controlador PID en tiempo discreto es:

C(z) = Kp +

Ki∆t
z − 1

+

Kd
∆t

z − 1
z

(4.7)

y expresada en forma de IIR:

C(z) =

(
Kp + Ki∆t +

Kd
∆t

)
+

(
−Kp −

2Kd
∆t

)
z

−1 +

Kd
∆t

z

−2
1 − z

−1

(4.8)

de la cual se puede deducir el bucle de control implementado habitualmente en PLCs y FPGAs.

A0 := Kp + Ki * dt + Kd / dt
A1 := -Kp - 2 * Kd / dt
A2 := Kd / dt
error[2] := 0
error[1] := 0
error[0] := 0
output := u0 // Normalmente el valor inicial del actuador start:
error[2] := error[1]
error[1] := error[0]
error[0] := setpoint - measured_value
output := A0 * error[0] + A1 * error[1] + A2 * error[2] wait(dt)
goto start

### 4.1.3. Filtro pasa baja en el término derivativo

El término derivativo de un controlador PID en tiempo discreto puede causar problemas de ruido en la señal de control, debido a cambios bruscos de la señal de error (flancos de subida o bajada). Para evitar estos problemas, se puede añadir un filtro pasa baja a la acción derivativa de constante de tiempo τ = Td/N, con 3 <= N <= 10, cuya expresión es:

C(z) = 1
τz−1 + 1

(4.9)

EPSE - Campus Terra (Lugo) | 15 / 63 | e.comesana@usc.es

y la ecuación del controlador PID con filtro pasa baja es:

C(z) = Kp +

Ki∆t
z − 1

+

KdTd
∆tN

z

−1

z

−1 + 1

(4.10)

El pseudocódigo que implementa este tipo de controlador PID, con filtro pasa baja, es:

A0 := Kp + Ki*dt
A1 := -Kp
error[2] := 0 // e(t-2)
error[1] := 0 // e(t-1)
error[0] := 0 // e(t)
output := u0 // Normalmente el valor inicial del actuador A0d := Kd/dt
A1d := - 2.0*Kd/dt
A2d := Kd/dt
N := 5
tau := Kd / (Kp*N) // Constante de tiempo del filtro pasa baja alpha := dt / (2*tau)
alpha_1 = alpha / (alpha + 1)
alpha_2 = (alpha - 1) / (alpha + 1)
d0 := 0
d1 := 0
fd0 := 0
fd1 := 0
loop:
error[2] := error[1]
error[1] := error[0]
error[0] := setpoint - measured_value
// PI
output := output + A0 * error[0] + A1 * error[1]
// Filtered D
d1 := d0
d0 := A0d * error[0] + A1d * error[1] + A2d * error[2] fd1 := fd0
fd0 := alpha_1 * (d0 + d1) - alpha_2 * fd1
output := output + fd0
wait(dt)
goto loop

## 4.2. Tareas a realizar

Implementar los tres pseudocódigos anteriores en el microcontrolador ESP32, empleado para la realización del proyecto del péndulo invertido (ver capítulo 6).

Integrar los código realizados en una biblioteca de control PID de vuestra realización. A modo de guía para crear la biblioteca, se puede seguir el tutorial de la realización de una biblioteca en C++ para Arduino en https://www.arduino.cc/en/Hacking/libraryTutorial o de forma más resumida en https://sp.arduino-france.site/crear-libreria/. En el caso de ESP32, se puede seguir el tutorial anterior si se emplea el entorno de desarrollo de Arduino.

Realizar pruebas de funcionamiento de los controladores PID implementados en el péndulo invertido construido.

Publicar el código de las librerías realizadas en el repositorio de GitHub del proyecto del péndulo invertido.

EPSE - Campus Terra (Lugo) | 16 / 63 | e.comesana@usc.es

## Práctica 5. Modelado de sistemas en el espacio de estados

Matlab proporciona un toolbox muy potente (Control System Toolbox). Este toolbox consiste en una colección de funciones que implementan técnicas para el diseño, análisis y modelado de sistemas de control lineales invariantes en el tiempo (LTI: Linear Time-Invariant). Sus características son:

Los sistemas de control pueden modelarse como funciones de transferencia o en el espacio de estados, permitiendo el uso tanto de técnicas de espacio de estados (control moderno) como de funciones de transferencia (control clásico).

Permite trabajar tanto con sistemas continuos como discretos.

Se pueden realizar conversiones entre las distintas representaciones de los sistemas.

Es posible calcular y representar respuestas en el dominio del tiempo, en el dominio de la frecuencia, así como el lugar de las raices.

Dispone de funciones para la asignación de polos, el control óptimo, etc.

Dispone de una interfaz gráfica (LTI Viewer) para el análisis de la respuesta de los sistemas.

## 5.1. Creación del modelo de un sistema continuo en el espacio de estados

Un sistema de control LTI se modela en Matlab como un objeto. Este objeto es una estructura de datos que permite manipular el modelo del sistema como si fuera una única variable Matlab.

Para definir un sistema continuo LTI con la siguiente representación:

¨⃗x(t) = A⃗x(t) + B⃗u(t)

⃗y(t) = C⃗x(t) + D⃗u(t)

podemos usar la función ss (https://es.mathworks.com/help/control/ref/ss.html) es decir, supongamos un sistema, con las siguientes ecuaciones de estado y salida:
[
x¨1(t)
x¨1(t)

]
=

[
0 1

−2 3]
·

[
x1(t)
x1(t)

]
+

[
0
1

]
- u(t)

y(t) = [

6 0]
·

[
x1(t)
x1(t)

]

A = [0 1; -2 3];
B = [0 1]';
C = [6 0];
D = 0;
sys = ss(A, B, C, D)

Esto ha creado un objeto llamado sys, correspondiente al sistema con las ecuaciones mostradas. La variable sys creada es una estructura de datos específica del modelo que permite manipular el sistema como una entidad única. Si quisiéramos extraer los datos asociados modelo, hay dos opciones:

1. Empleando la función ssdata (https://es.mathworks.com/help/ident/ref/dynamicsystem.ssdata.html)

[A, B, C, D] = ssdata(sys)

EPSE - Campus Terra (Lugo) | 17 / 63 | e.comesana@usc.es

2. Accediendo directamente a las propiedades del objeto con el modelo del sistema:

matriz = sys.A;

la variable matriz contiene la matriz de estado del modelo sys.

### 5.1.1. Conversión de modelos entre representación interna y externa

Para convertir un sistema entre distintas representaciones se utilizan las mismas funciones que para crear los modelos. Por ejemplo, para obtener el modelo del sistema en representación externa (función de transferencia) a partir de su modelo en representación interna (ecuanciones de estado), se ejecutaría en Matlab:

systf = tf(sys)

donde sys es el sistema modelado en el espacio de estados y systf el modelo en forma de función de transferencia. Para realizar la operación inversa:

sys = ss(systf)

### 5.1.2. Cálculo y visualización de la respuesta del sistema

El toolbox de control de Matlab también permite obtener la representación gráfica de la salida de un sistema para diferentes tipos de entradas:

Función step: (https://es.mathworks.com/help/control/ref/dynamicsystem.step.html) Respresenta gráficamente la respuesta del sistema ante una entrada escalón unitario, asumiendo que las condiciones iniciales son nulas.

step(sys)

[y, t, x] = step(sys);
% y es la respuesta del sistema
% t vector del tiempo de simulacion
% x evolucion de las variables de estado plot(t, x)

Función initial: (https://es.mathworks.com/help/control/ref/lti.initial.html) Respuesta del sistema ante unas condiciones iniciales determinadas, x0, considerando que la entrada es nula:

initial(sys, x0)
% o
[y, t, x] = initial(sys, x0)

Función lsim: (https://es.mathworks.com/help/control/ref/dynamicsystem.lsim.html) Obtiene la respuesta ante una entrada arbitraria.

lsim(sys, u, t, x0)
% o
[y, ts, x] = lsim(sys, u, t, x0)

donde t es el vector de tiempo de los datos de entrada que se expresan en u. x0 son las condiciones iniciales, si se asumen nulas no es necesario incluirlas.

El toolbox incorpora una interfaz interactiva que facilita el análisis de la respuesta de los modelos LTI, denominada LTI Viewer. Para abrir esta herramienta, ejecutar en Matlab: ltiview (https://es.mathworks.com/help/control/ug/basic-lti-viewer-tasks.html)

La interfaz permite obtener la respuesta de cualquier sistema definido ante diferentes señales de entrada.

EPSE - Campus Terra (Lugo) | 18 / 63 | e.comesana@usc.es

### 5.1.3. Cuestiones

Sea el sistema continuo definido en su representación interna por:

¨⃗x(t) =

0 | 1 | 0
0 | 0 | 1
−50 −20 −10

- · ⃗x(t) +

0
0
1

- · ⃗u(t)

⃗y(t) = [

30 0 0]
- ⃗x(t)

Utilizando las funciones necesarias:

1. Representar el sistema como un objeto LTI.
2. Obtener la respuesta del sistema, la evolución de las variables de estado, considerando una entrada escalón unitario y condiciones iniciales nulas.
3. Obtener la respuesta del sistema y la evolución de las variables de estado, considerando con-diones iniciales x0 = [0, 5, −1] y entrada nula.
4. Obtener la respuesta del sistema y evolución de los estados ante una entrada escalón unitario y condiciones inicales x0 = [0, 5, −1].
5. Obtener la respuesta del sistema cuando la entrada es como la que se muestra en la figura y suponiendo condiciones iniciales nulas

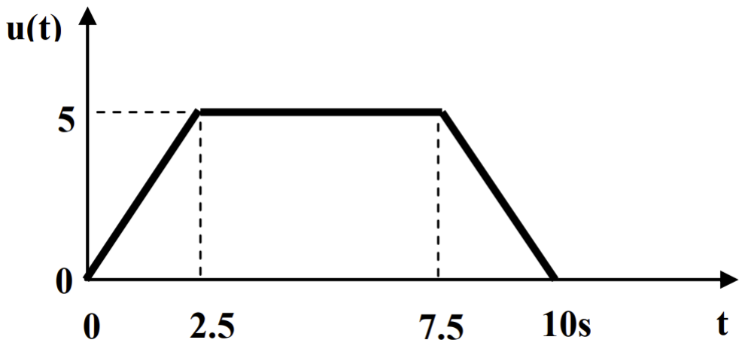
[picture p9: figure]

6. Obtener la función de transferencia del sistema y la salida de dicha función ante un escalón unitario, comprobar que el resultado coincide con la 2ª cuestión.

## 5.2. Controlabilidad y observabilidad de un sistema

En Matlab podemos evaluar la controlabilidad del estado de un sistema usando la función ctrb, (https://es.mathworks.com/help/control/ref/ss.ctrb.html) que devuelve la matriz de controlabilidad del sistema y evaluando su rango con la función rank (https://es.mathworks.com/help/matlab/ref/rank.html) podemos determinar si un sistema es o no controlable.

Del mismo modo con la función obsv (https://es.mathworks.com/help/control/ref/ss.obsv.html) se obtiene la matriz de observabilidad y con ella podremos evaluar si el estado de un sistema es o no observable a partir de un conjunto de salidas.

### 5.2.1. Cuestiones

Usando la descrición del sistema del apartado anterior

1. Obtener la matriz de observabilidad y de controlabilidad del sistema:
EPSE - Campus Terra (Lugo) | 19 / 63 | e.comesana@usc.es

a) Empleando las funciones ctrb (https://es.mathworks.com/help/control/ref/ss.ctrb.html) y obsv. (https://es.mathworks.com/help/control/ref/ss.obsv.html)
b) Realizando el cálculo sin emplear las funciones anteriores, solo operaciones básicas con matrices.

Comprobar que el resultado es el mismo por ambos métodos.

2. Evaluar si el sistema es observable y controlable.

## 5.3. Modelo de estados del robot Turtlebot (opcional)

Un robot con ruedas es aquel que funciona en contacto con el suelo y su movimiento se basa en ruedas accionadas por separado situadas a ambos lados del cuerpo del robot. Así, puede cambiar de dirección variando la velocidad relativa de rotación de sus ruedas. En general, independientemente del número de ruedas que tenga, la velocidad de cada lado tendrá el mismo valor por separado. Por lo tanto, todos los robots con ruedas pueden ser tratados como robots de tracción diferencial con dos ruedas.

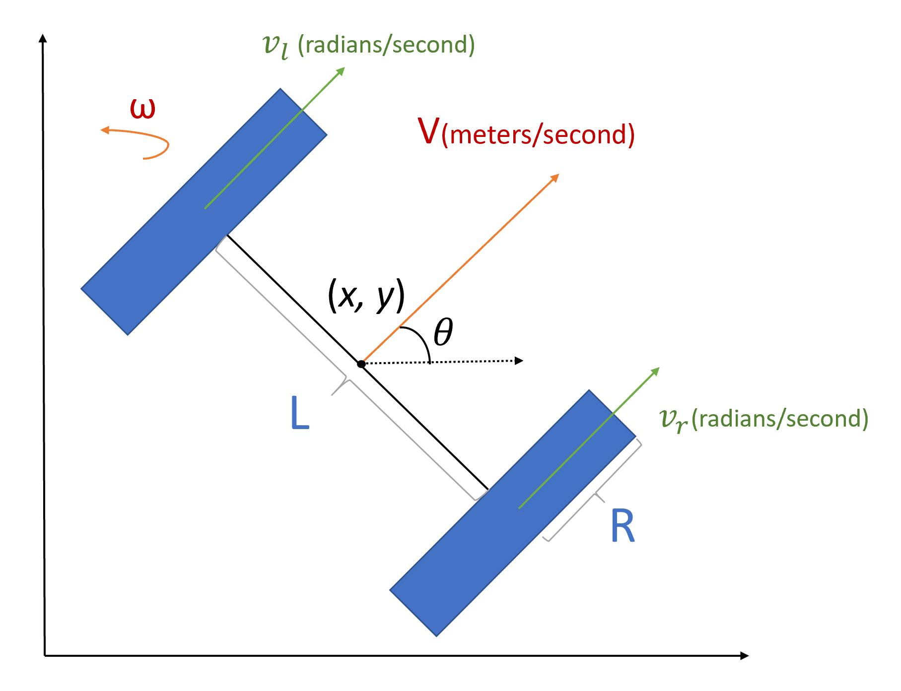
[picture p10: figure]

Si se está diseñando un robot físico y se necesita conocer las verdaderas entradas a las ruedas, es necesario modelar un robot de tracción diferencial. El diferencial de tracción es un sistema de tracción de dos ruedas con actuadores independientes. Normalmente se colocan dos ruedas motrices a cada lado del robot y la dirección hacia el frente se trata como la dirección positiva. Tendrá un estado

EPSE - Campus Terra (Lugo) | 20 / 63 | e.comesana@usc.es

definido por las variables (x, y, θ), que será la posición y dirección del robot en todo instante, y las entradas de este sistema mecánico serán las velocidades de la rueda izquierda (vl) y derecha (vr).

Ref: https://ucr-robotics.readthedocs.io/en/latest/tbot/moRbt.html

## 5.4. Cuestiones

1. Teniendo en cuenta lo anteriormente descrito, plantea un modelo de estados para el movimiento del Turtlebot, usando como variables de entrada y salida las descritas anteriormente. Tener en cuenta que la distancia entre ruedas es L = 23cm y el diametro de las ruedas es de R = 3, 5 cm
2. Teniendo en cuenta la información disponible para las características de los motores que accio-nan las ruedas del Turtlebot, construye un modelo de estados para el sistema electromecánico de accionamiento. Las características del modelo de motor en el Turtlebot, están en “Kobuki User Guide” disponible en el anexo B.
EPSE - Campus Terra (Lugo) | 21 / 63 | e.comesana@usc.es

## Práctica 6. Proyecto péndulo invertido

El objetivo de esta tarea es que durante la duración de la materia realices la construcción de un péndulo invertido y su control. El péndulo invertido es un sistema no lineal, inestable y de doble integración. La inestabilidad del sistema hace que sea un problema interesante para el control, ya que el controlador debe ser capaz de estabilizar el sistema y mantenerlo en una posición vertical.

## 6.1. Objetivos

Elegir y adquirir componentes electromecánicos y electronicos para el proyecto.

Diseñar e imprimir/fabricar el sistema mecánico del péndulo invertido mediante impresión 3D, corte laser u otra técnica adecuada.

Diseñar e implementar el controlador del péndulo invertido. Diseño de PCB, fabricación y soldadura de componentes.

Realizar la implementación del software de control en el microcontrolador ESP32 o Arduino nano.

Sintonizar y ajustar el control PID para el péndulo invertido.

Cumplir las especificaciones a continuación para el sistema completo.

## 6.2. Especificaciones

El sistema debe ser capaz de mantenerse en posición vertical con una tolerancia de ±5

◦

El sistema debe compensar los empujones externos y volver a la posición vertical.

El sistema debe ser capaz de poder iniciar su funcionamiento desde cualquier posición.

## 6.3. Entregables

Repositorio en GitHub con la descripción del sistema, diseño y elementos necesarios para la fabricación de la estructura, diseños y elementos para fabricación de la PCB, implementación del software y sintonización del controlador.

El repositorio debe contener un informe en formato markdown en el fichero README.md del propio repositorio, siguiendo la línea del ejemplo mostrado a continuación.

Demostración del sistema funcionando en una fecha anterior al final de la materia.

## 6.4. Aclaraciones

Para la realización del diseño de partes mecánicas del péndulo invertido, se deberá un de software de diseño 3D “profesional”, como puede ser Fusion 360, FreeCAD, Catia, SolidWorks,

EPSE - Campus Terra (Lugo) | 22 / 63 | e.comesana@usc.es

etc. No se aceptarán diseños realizados en Tinkercad o similares. Se puede acceder a cuentas gratuitas de estudiantes para Fusion 360 (y el resto del software de Autodesk) en https: //www.autodesk.com/education/home, registrándose con el correo de la USC. Todos los proyectos deben incluir algún componente mecánico de diseño y fabricación propia.

Para la fabricación de las piezas mecánicas, se puede usar cualquier técnica de fabricación, como por ejemplo impresión 3D, corte laser, etc. La escuela dispone de un taller de fabricación con impresoras 3D y cortadoras laser y otras herramientas: Laboratorio de Instrumentación. Para poder acceder solicitarlo al profesor de la materia.

Para realizar el diseño de la PCB (esquemático, pcb y ficheros de fabricación) utilizar el software de diseño de PCBs KiCad. (https://www.kicad.org/) No se aceptarán montajes con elementos electrónicos sueltos o montados en protoboard.

Para la fabricación de la PCB, se puede usar cualquier servicio de fabricación de PCBs, como por ejemplo JLCPCB, (https://https://jlcpcb.com/) PCBWay, (https://www.pcbway.com) etc. Existe una web donde se pueden comparar los precios de diferentes fabricantes de PCBs: https://pcbshopper.com/.

## 6.5. Ejemplo de informe

Para que os sirva de guia a la hora de realizar el proyecto y preparar una documentación, os adjunto, en el anexo A, un ejemplo de informe de la realización hecha por Daniel Acevedo de este proyecto de péndulo invertido.

EPSE - Campus Terra (Lugo) | 23 / 63 | e.comesana@usc.es

## Anexo A. Ejemplo de informe del proyecto péndulo invertido

Ejemplo de informe sobre el proyecto/práctica a realizar sobre el péndulo invertido. Este documento debe servir de guía tanto para la realización del proyecto como para la preparación de la documentación a anexar en el repositorio de GitHub del proyecto realizado.

Siendo una guía, se tendrá en cuenta que cada proyecto es diferente y por lo tanto, la documentación a entregar también lo será. Por lo tanto, este ejemplo de informe debe ser tomado como una guía y no como un documento a copiar y entregar.

EPSE - Campus Terra (Lugo) | 24 / 63 | e.comesana@usc.es

### P´endulo Invertido

Daniel Acevedo Facal

14 de diciembre de 2023

### 1. Introducci´on

En este documento se recoge la creaci´on de un primer prototipo de un robot tipo ”p´endulo invertido”.

### 2. Metodolog´ıa seguida

1. Buscar proyectos similares:
Investigar si ya existe un proyecto de un robot similar que est´e funcional y documentado.
2. Investigaci´on general:
Como no existe ning´un proyecto bien hecho y bien documentado, procedemos a investigar c´omo podemos llevar a cabo el proyecto desde cero.
3. Fijaci´on de objetivos:
Es importante tener metas para saber qu´e hardware necesitamos.
4. Selecci´on del Hardware:
Una vez que sabemos qu´e queremos lograr con nuestro robot, tenemos que buscar el hardware con las caracter´ısticas necesarias.
5. Dise˜no del Chasis:
En este apartado debemos resolver dos problem´aticas: tener el peso compensado y tener el centro de gravedad bajo.
6. Prueba de componentes por separado:
Verificamos que todo funcione por separado para luego juntar todo.
7. Montaje: Montamos todos los componentes en el chasis para poder probar el robot al completo.
8. Programaci´on inicial:
Hacemos un primer c´odigo que solo mantenga el robot est´atico en un mismo lugar.
9. Ajuste del PID:
Ajustamos los valores del PID para que el robot se mantenga est´atico.
10. Implementaci´on de control por mando:
Realizamos un c´odigo que nos permita desplazar el robot con un mando Bluetooth.

### 3. Objetivos

1. Estabilidad Perpendicular al Suelo: Garantizar que el robot sea capaz de mantenerse estable en posici´on perpendicular al suelo. Logrado
2. Compensaci´on de Empujones:
Desarrollar la capacidad del robot para compensar empujones y evitar ca´ıdas. Logrado
3. Arranque desde Cualquier Posici´on:
Lograr que el robot pueda iniciar su funcionamiento desde cualquier posici´on inicial. Logrado
4. Reducci´on de Posibilidades de Volcar:
Minimizar las posibilidades de volcamiento y asegurar que el robot no pueda volver a la posici´on incorrecta. Logrado
5. Control mediante Mando Bluetooth:
Implementar un sistema de control que permita manejar el robot a trav´es de un mando Bluetooth.

### 4. Investigaci´on

En relaci´on con la b´usqueda de otros proyectos de este estilo, he detectado una problem´atica: hay varios proyectos hechos con el mismo principio, pero nadie ha creado una documentaci´on del proyecto para ayudar a otras personas que quieran hacerlo. Por lo tanto, tuve que empezar casi desde cero. Aunque hay esta escasez de informaci´on, he podido rescatar algo de informaci´on examinando fotos y v´ıdeos. De ellos, he determinado el hardware que se necesita y el tipo de control para manejar el movimiento (PID).

### 5. Hardware

Para la selecci´on del hardware, se busc´o que el robot se hiciera con elementos b´asicos y comunes para que sea un robot de bajo costo.

1. ESP32:
Para el microcontrolador, he elegido una ESP32, la cual me permitir´a conectar un mando a ella mediante Bluetooth e incluso se podr´ıa usar su conectividad WiFi para diversas funciones. En concreto, se ha utilizado una ESP32-devkitc-v4 que ronda los 5€.

He consultado un par de p´aginas web para informarme al respecto de esta placa, para no alargar este documento dejo los enlaces a continuaci´on: enlace01, enlace02.

2. MPU-6050:
Este sensor tiene incorporado un aceler´ometro y un giroscopio, los cuales vamos a usar para medir la orientaci´on del robot. Las f´ormulas e informaci´on necesaria que he necesitado para usar este sensor est´an en esta p´agina web.
3. TB6612FNG:
El driver que he elegido es una soluci´on m´as moderna que el com´un puente H; su precio es de menos de 2€ y nos permite controlar 2 motores simult´aneamente y de manera independiente. Al igual que con el anterior sensor, la p´agina de la que extraje toda la informaci´on la dejo en el siguiente enlace.
4. Regulador de tensi´on:
Pendiente de documentar lo que se us´o en este aspecto.
5. Bater´ıa:
Primero se realiz´o el robot con un portapilas de 4 pilas AA, pero posteriormente se ha implementado una bater´ıa LiPo que nos proporciona m´as autonom´ıa y facilidad a la hora de recargar el robot.
6. Motores y ruedas:
En este proyecto se han usado los com´unmente usados motores de DC con una reductora, la cual permite un f´acil acople de una rueda que normalmente se vende con el propio motor.

### 6. Chasis

He dise˜nado 4 chasis para el robot, y con el tercero he logrado hacer funcionar el robot. En el desarrollo de estos 3 chasis, he podido valorar cu´ales son los factores determinantes para que el robot funcione.

1. Centro de gravedad:
Es determinante que el centro de gravedad del robot sea el m´as bajo posible. Si el peso est´a muy elevado respecto al suelo, se har´a pr´acticamente imposible que el robot sea capaz de mantenerse derecho.
2. Peso centrado:
Al igual que el centro de gravedad bajo, es decisivo que el peso del robot est´e centrado en el eje de las ruedas, lo que har´a que, combinado con el apartado anterior, el robot deber´ıa mantenerse en la posici´on que queremos sin necesidad de que el robot est´e encendido. Cuanto m´as estable sea el robot gracias al dise˜no del chasis, m´as sencillo nos ser´a ajustar el PID hasta lograr que el robot funcione correctamente.

Ahora voy a explicar los problemas de mis distintos chasis hasta el momento en que fui capaz de hacer que el robot funcionara.

1. Primer chasis:
Este estaba bastante mal hecho, ya que el centro de gravedad estaba demasiado alto, lo que hac´ıa muy complicado que el robot fuese capaz de mantenerse en posici´on vertical.

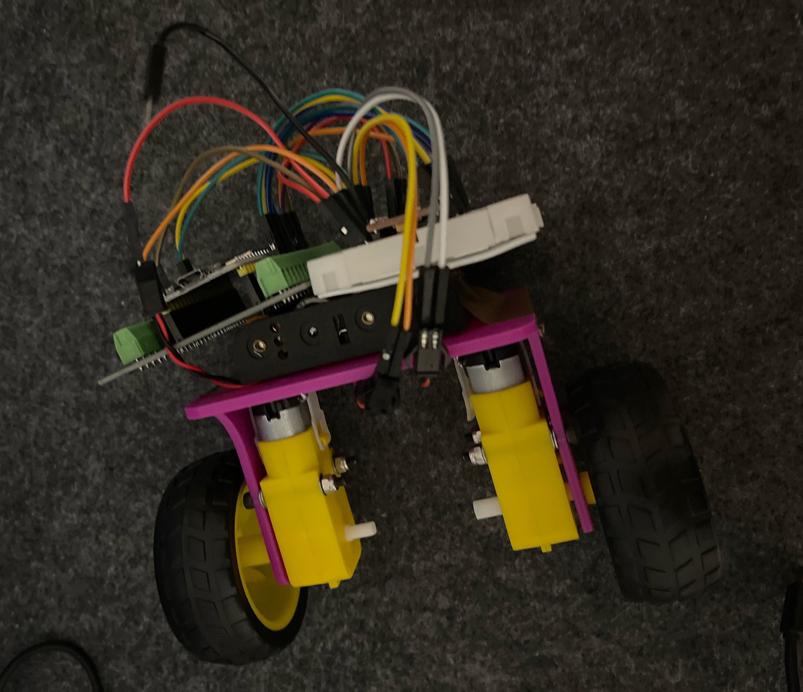
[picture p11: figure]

Figura 1: Chasis01

2. Segundo chasis:
Aunque el centro de gravedad era m´as bajo en este segundo chasis, el problema fue que el peso no estaba centrado, y el robot tend´ıa a inclinarse hacia un lado constantemente.
3. Tercer chasis:
Despu´es de corregir los errores de los dos chasis anteriores, logr´e que el robot funcionara. En este caso, el centro de gravedad estaba muy centrado y a una altura baja, lo que proporcionaba una gran estabilidad incluso cuando el robot estaba apagado.

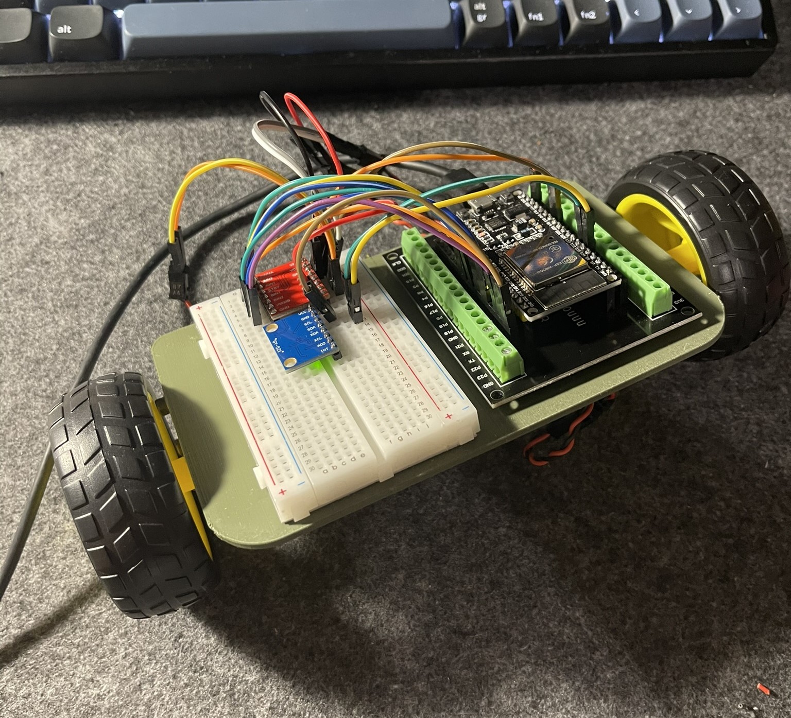
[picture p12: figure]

Figura 2: Chasis03

4. Cuarto chasis:
Este chasis (foto de la portada) me permite incorporar una bater´ıa LiPo sin dejar de tener en cuenta las caracter´ısticas del anterior, que ya funcionaba con pilas.

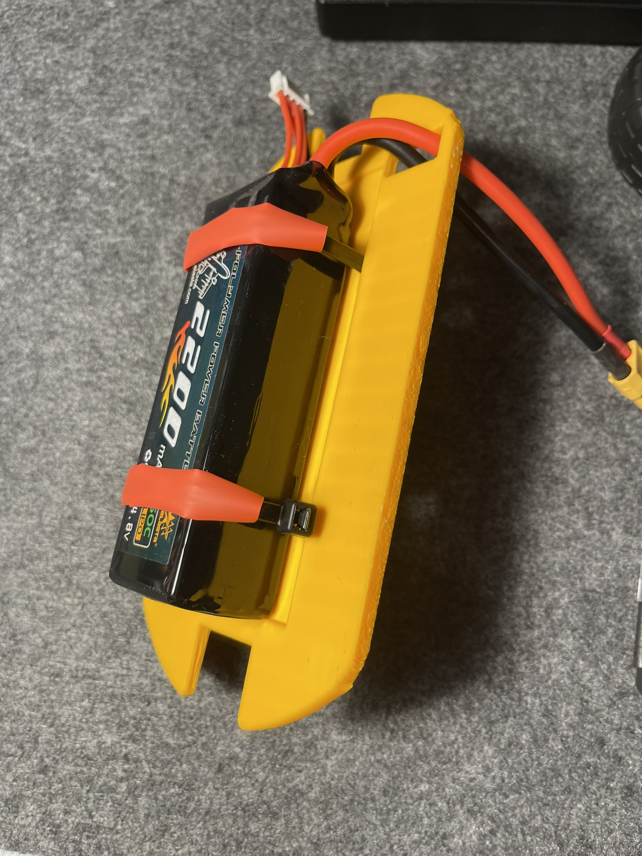
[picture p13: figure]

Figura 3: Chasis04 parte inferior

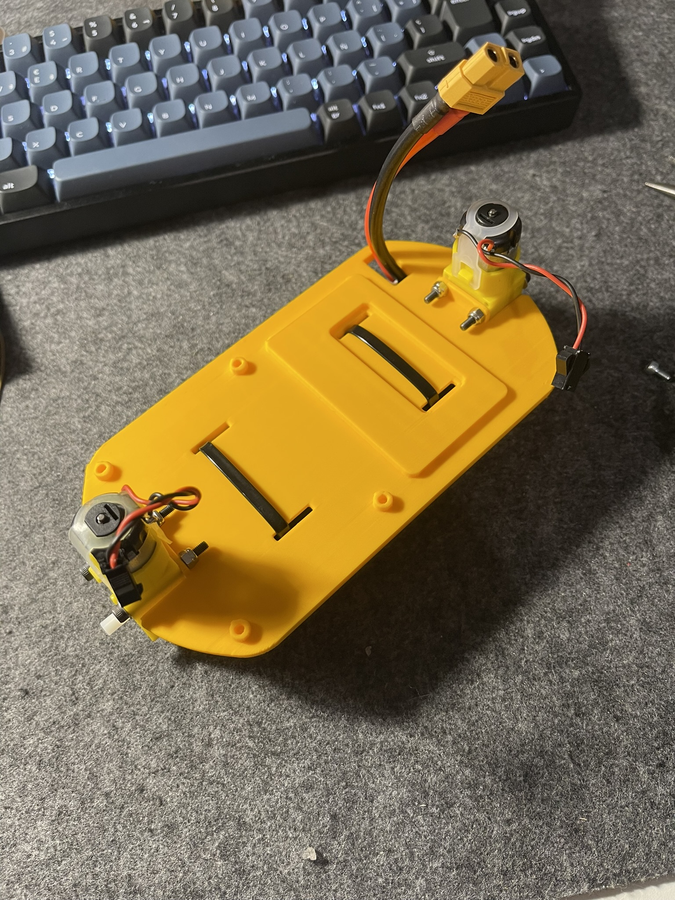
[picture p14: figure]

Figura 4: Chasis04 parte superior

### 7. Prueba de componentes por separado

MPU-6050:
Realizamos una primera prueba para verificar que el sensor funcione.
1 | // Librerias I2C para controlar el mpu6050
2 | // la libreria MPU6050 .h necesita I2Cdev .h, I2Cdev .h necesita Wire .h
3 | # include " I2Cdev .h"
4 | # include " MPU6050 .h"
5 | # include " Wire .h"

6
7 | // La d i r e c c i n del MPU6050 puede ser 0 x68 o 0x69 , dependiendo
8 | // del estado de AD0 . Si no se especifica , 0 x68 e s t a r | implicito
9 | MPU6050 sensor ;

10
11 | // Valores RAW ( sin procesar ) del acelerometro y giroscopio en los ejes x,y,z
12 | int ax , ay , az ;
13 | int gx , gy , gz ;

14
15 | void setup () {
16 | Serial . begin (57600) ; | // Iniciando puerto serial
17 | Wire . begin () ; | // Iniciando I2C
18 | sensor . initialize () ; | // Iniciando el sensor

19
20 | if ( sensor . testConnection () ) Serial . println (" Sensor iniciado correctamente ");
21 | else Serial . println (" Error al iniciar el sensor ");
22 | }

23
24 | void loop () {
25 | // Leer las aceleraciones y velocidades angulares
26 | sensor . getAcceleration (& ax , & ay , & az ) ;
27 | sensor . getRotation (& gx , & gy , & gz );

28
29 | // Mostrar las lecturas separadas por un [tab]
30 | Serial . print ("a[x y z] g[x y z ]:\ t");

31 | Serial . print ( ax ); Serial . print ("\t");
32 | Serial . print ( ay ); Serial . print ("\t");
33 | Serial . print ( az ); Serial . print ("\t");
34 | Serial . print ( gx ); Serial . print ("\t");
35 | Serial . print ( gy ); Serial . print ("\t");
36 | Serial . println ( gz );

37
38 | delay (100) ;
39 | }
Listing 1: C´odigo para probar el MPU6050

Como vemos que el sensor nos proporciona medidas coherentes, procedemos a calibrar el sensor en la posici´on en la que estar´a midiendo.

1 | // Librerias I2C para controlar el mpu6050
2 | // la libreria MPU6050 .h necesita I2Cdev .h, I2Cdev .h necesita Wire .h
3 | # include " I2Cdev .h"
4 | # include " MPU6050 .h"
5 | # include " Wire .h"

6
7 | // La d i r e c c i n del MPU6050 puede ser 0 x68 o 0x69 , dependiendo
8 | // del estado de AD0 . Si no se especifica , 0 x68 e s t a r | implicito
9 | MPU6050 sensor ;

10
11 | // Valores RAW ( sin procesar ) del acelerometro y giroscopio en los ejes x,y,z
12 | int ax , ay , az ;
13 | int gx , gy , gz ;

14
15 | // Variables usadas por el filtro pasa bajos
16 | long f_ax , f_ay , f_az ;
17 | int p_ax , p_ay , p_az ;
18 | long f_gx , f_gy , f_gz ;
19 | int p_gx , p_gy , p_gz ;
20 | int counter =0;

21
22 | // Valor de los offsets
23 | int ax_o , ay_o , az_o ;
24 | int gx_o , gy_o , gz_o ;

25
26 | void setup () {
27 | Serial . begin (57600) ; | // Iniciando puerto serial
28 | Wire . begin () ; | // Iniciando I2C
29 | sensor . initialize () ; | // Iniciando el sensor

30
31 if ( sensor . testConnection () ) Serial . println (" Sensor iniciado correctamente ");

32
33 | // Leer los offset los offsets anteriores
34 | ax_o = sensor . getXAccelOffset () ;
35 | ay_o = sensor . getYAccelOffset () ;
36 | az_o = sensor . getZAccelOffset () ;
37 | gx_o = sensor . getXGyroOffset () ;
38 | gy_o = sensor . getYGyroOffset () ;
39 | gz_o = sensor . getZGyroOffset () ;

40
41 | Serial . println (" Offsets :") ;
42 | Serial . print ( ax_o ); Serial . print ("\t") ;
43 | Serial . print ( ay_o ); Serial . print ("\t") ;
44 | Serial . print ( az_o ); Serial . print ("\t") ;
45 | Serial . print ( gx_o ); Serial . print ("\t") ;
46 | Serial . print ( gy_o ); Serial . print ("\t") ;
47 | Serial . print ( gz_o ); Serial . print ("\t") ;
48 | Serial . println (" nnEnvie cualquier caracter para empezar la calibracionnn ") ;
49 | // Espera un caracter para empezar a calibrar
50 | while ( true ){if ( Serial . available () ) break ;}
51 | Serial . println (" Calibrando , no mover IMU ");

52
53 }

54
55 | void loop () {
56 | // Leer las aceleraciones y velocidades angulares
57 | sensor . getAcceleration (& ax , & ay , & az ) ;

58 sensor . getRotation (& gx , & gy , & gz );

59
60 | // Filtrar las lecturas
61 | f_ax = f_ax -( f_ax > >5) + ax ;
62 | p_ax = f_ax > >5;

63
64 | f_ay = f_ay -( f_ay > >5) + ay ;
65 | p_ay = f_ay > >5;

66
67 | f_az = f_az -( f_az > >5) + az ;
68 | p_az = f_az > >5;

69
70 | f_gx = f_gx -( f_gx > >3) + gx ;
71 | p_gx = f_gx > >3;

72
73 | f_gy = f_gy -( f_gy > >3) + gy ;
74 | p_gy = f_gy > >3;

75
76 | f_gz = f_gz -( f_gz > >3) + gz ;
77 | p_gz = f_gz > >3;

78
79 | // Cada 100 lecturas corregir el offset
80 | if ( counter ==100) {
81 | // Mostrar las lecturas separadas por un [tab]
82 | Serial . print (" promedio :"); Serial . print ("t");
83 | Serial . print ( p_ax ); Serial . print ("\t") ;
84 | Serial . print ( p_ay ); Serial . print ("\t") ;
85 | Serial . print ( p_az ); Serial . print ("\t") ;
86 | Serial . print ( p_gx ); Serial . print ("\t") ;
87 | Serial . print ( p_gy ); Serial . print ("\t") ;
88 | Serial . println ( p_gz );

89
90 | // Calibrar el acelerometro a 1g en el eje z ( ajustar el offset )
91 | if ( p_ax >0) ax_o - -;
92 | else { ax_o ++;}
93 | if ( p_ay >0) ay_o - -;
94 | else { ay_o ++;}
95 | if ( p_az -16384 >0) az_o - -;
96 | else { az_o ++;}

97
98 | sensor . setXAccelOffset ( ax_o );
99 | sensor . setYAccelOffset ( ay_o );
100 | sensor . setZAccelOffset ( az_o );

101
102 | // Calibrar el giroscopio a 0 | /s en todos los ejes ( ajustar el offset )
103 | if ( p_gx >0) gx_o - -;
104 | else { gx_o ++;}
105 | if ( p_gy >0) gy_o - -;
106 | else { gy_o ++;}
107 | if ( p_gz >0) gz_o - -;
108 | else { gz_o ++;}

109
110 | sensor . setXGyroOffset ( gx_o );
111 | sensor . setYGyroOffset ( gy_o );
112 | sensor . setZGyroOffset ( gz_o );

113
114 | counter =0;
115 | }
116 | counter ++;
117 | }
Listing 2: C´odigo para calibrar el MPU6050

Finalmente, probamos el c´odigo que utilizaremos para medir el ´angulo de inclinaci´on del robot.

1 | // Librerias I2C para controlar el mpu6050
2 | // la libreria MPU6050 .h necesita I2Cdev .h, I2Cdev .h necesita Wire .h
3 | # include " I2Cdev .h"
4 | # include " MPU6050 .h"
5 | # include " Wire .h"

6
7 // La d i r e c c i n del MPU6050 puede ser 0 x68 o 0x69 , dependiendo

8 | // del estado de AD0 . Si no se especifica , 0 x68 e s t a r | implicito
9 | MPU6050 sensor ;

10
11 | // Valores RAW ( sin procesar ) del acelerometro y giroscopio en los ejes x,y,z
12 | int ax , ay , az ;
13 | int gx , gy , gz ;
14 | long tiempo_prev ;
15 | float dt ;
16 | float ang_x , ang_y ;
17 | float ang_x_prev , ang_y_prev ;

18
19 | void setup () {
20 | Serial . begin (57600) ; | // Iniciando puerto serial
21 | Wire . begin () ; | | // Iniciando I2C
22 | sensor . initialize () ; | // Iniciando el sensor

23
24 | if ( sensor . testConnection () ) Serial . println (" Sensor iniciado correctamente ");
25 | else Serial . println (" Error al iniciar el sensor ");
26 | }

27
28 | void loop () {
29 | // Leer las aceleraciones y velocidades angulares
30 | sensor . getAcceleration (& ax , & ay , & az ) ;
31 | sensor . getRotation (& gx , & gy , & gz );

32
33 | dt = ( millis () - tiempo_prev ) /1000.0;
34 | tiempo_prev = millis () ;

35
36 | // Calcular los | ngulos | con acelerometro
37 | float accel_ang_x = atan ( ay / sqrt ( pow (ax ,2) + pow ( az ,2) )) *(180.0/3.14) ;
38 | float accel_ang_y = atan (- ax / sqrt ( pow ( ay ,2) + pow (az ,2) )) *(180.0/3.14) ;

39
40 | // Calcular angulo de r o t a c i n con giroscopio y filtro complemento
41 | ang_x = 0.98*( ang_x_prev +( gx /131) * dt ) + 0.02* accel_ang_x ;
42 | ang_y = 0.98*( ang_y_prev +( gy /131) * dt ) + 0.02* accel_ang_y ;

43

44
45 | ang_x_prev = ang_x ;
46 | ang_y_prev = ang_y ;

47
48 // Mostrar los angulos separadas por un [ tab ]

49
50 | Serial . print (" Rotacion en X: | ");
51 | Serial . print ( ang_x );
52 | Serial . print (" tRotacion en Y: ");
53 | Serial . println ( ang_y ) ;

54
55 | delay (10) ;
56 | }
Listing 3: C´odigo completo MPU 6050

Estos c´odigos han sido extra´ıdos de la p´agina web antes citada.

TB6612FNG:
Vamos a probar con un c´odigo b´asico extra´ıdo de la p´agina web citada en la secci´on de hardware. Al igual que los c´odigos del sensor anterior, los he modificado antes de subirlos a la ESP32, ajustando los pines para que sean compatibles con la ESP32.
1 | const int pinPWMA = 6;
2 | const int pinAIN2 = 7;
3 | const int pinAIN1 = 8;
4 | const int pinBIN1 = 9;
5 | const int pinBIN2 = 10;
6 | const int pinPWMB = 11;
7 | const int pinSTBY = 12;
8 | const int waitTime = 2000; | // espera entre fases
9 | const int speed = 200; | // velocidad de giro
10 | const int pinMotorA [3] = { pinPWMA , pinAIN2 , pinAIN1 };
11 | const int pinMotorB [3] = { pinPWMB , pinBIN1 , pinBIN2 };

12

13 | enum moveDirection {
14 | forward ,
15 | backward
16 | };

17
18 | enum turnDirection {
19 | clockwise ,
20 | counterClockwise
21 | };

22
23 | void setup ()
24 | {
25 | pinMode ( pinAIN2 , OUTPUT ) ;
26 | pinMode ( pinAIN1 , OUTPUT ) ;
27 | pinMode ( pinPWMA , OUTPUT ) ;
28 | pinMode ( pinBIN1 , OUTPUT ) ;
29 | pinMode ( pinBIN2 , OUTPUT ) ;
30 | pinMode ( pinPWMB , OUTPUT ) ;
31 | }

32
33 | void loop ()
34 | {
35 | enableMotors () ;
36 | move ( forward , 180) ;
37 | delay ( waitTime );

38
39 | move ( backward , 180) ;
40 | delay ( waitTime );

41
42 | turn ( clockwise , 180) ;
43 | delay ( waitTime );

44
45 | turn ( counterClockwise , 180) ;
46 | delay ( waitTime );

47
48 | fullStop () ;
49 | delay ( waitTime );
50 | }

51
52 | // Funciones que controlan el vehiculo
53 | void move ( int direction , int speed )
54 | {
55 | if ( direction == forward )
56 | {
57 | moveMotorForward ( pinMotorA , speed );
58 | moveMotorForward ( pinMotorB , speed );
59 | }
60 | else
61 | {
62 | moveMotorBackward ( pinMotorA , speed ) ;
63 | moveMotorBackward ( pinMotorB , speed ) ;
64 | }
65 | }

66
67 | void turn ( int direction , int speed )
68 | {
69 | if ( direction == forward )
70 | {
71 | moveMotorForward ( pinMotorA , speed );
72 | moveMotorBackward ( pinMotorB , speed ) ;
73 | }
74 | else
75 | {
76 | moveMotorBackward ( pinMotorA , speed ) ;
77 | moveMotorForward ( pinMotorB , speed );
78 | }
79 | }

80
81 | void fullStop ()
82 | {
83 | disableMotors () ;

84 | stopMotor ( pinMotorA );
85 | stopMotor ( pinMotorB );
86 | }

87
88 | // Funciones que controlan los motores
89 | void moveMotorForward ( const int pinMotor [3] , int speed )
90 | {
91 | digitalWrite ( pinMotor [1] , HIGH );
92 | digitalWrite ( pinMotor [2] , LOW );

93
94 | analogWrite ( pinMotor [0] , speed );
95 | }

96
97 | void moveMotorBackward ( const int pinMotor [3] , int speed )
98 | {
99 | digitalWrite ( pinMotor [1] , LOW );
100 | digitalWrite ( pinMotor [2] , HIGH );

101
102 | analogWrite ( pinMotor [0] , speed );
103 | }

104
105 | void stopMotor ( const int pinMotor [3])
106 | {
107 | digitalWrite ( pinMotor [1] , LOW );
108 | digitalWrite ( pinMotor [2] , LOW );

109
110 | analogWrite ( pinMotor [0] , 0) ;
111 | }

112
113 | void enableMotors ()
114 | {
115 | digitalWrite ( pinSTBY , HIGH );
116 | }

117
118 | void disableMotors ()
119 | {
120 | digitalWrite ( pinSTBY , LOW );
121 | }
Listing 4: C´odigo prueba del driver y motores

### 8. Montaje

El montaje es muy simple; las conexiones de los sensores que debemos realizar est´an explicadas en las p´aginas web mencionadas anteriormente. Adem´as de las conexiones de los sensores, necesitamos alimentar los motores y la ESP32. Ambos trabajan a voltajes distintos, por lo que requerimos dos reguladores de voltaje. Los motores los he alimentado a 9V, y la ESP32-DevKitC-v4 se alimenta a 5V en el pin 5V. Otros modelos se alimentan por el pin VIN a 3.3V, pero en este caso no es as´ı. El esquema el´ectrico bien hecho a´un no est´a listo; lo a˜nadir´e a esta documentaci´on cuando tenga la PCB lista.

### 9. Ajuste del PID

Para poder ajustar el PID, es necesario comprender la funci´on de cada una de las tres componentes de este sistema de control. He consultado esta p´agina para comprender c´omo funciona un PID. La forma de ajustar el PID est´a explicada en esa misma p´agina web, pero en otra secci´on, y la implementaci´on en c´odigo tambi´en se explica en otra secci´on. Cabe destacar que no consult´e esta ´ultima secci´on. Durante el proceso de calibraci´on del robot, he aprendido algunos ”truquitos”´utiles:

Empezar desde 0:
Es crucial comenzar con todos los valores desde 0 y ajustar los valores de manera ordenada e independiente.

Orden de calibraci´on:
Se recomienda iniciar ajustando los valores de Kp hasta lograr que el robot sea capaz de levan-tarse desde el suelo. Una vez logrado esto, se anota el valor que pareci´o ´optimo y se establece la variable a 0.
Luego, se ajusta Kd, buscando un valor en el cual el robot no oscile exageradamente y casi se mantenga en la posici´on deseada.
En el tercer paso, se restablece Kp al valor anotado anteriormente y se deja Kd en el valor ´optimo encontrado. En este punto, Ki a´un se mantiene en 0, pero primero se verifica que el robot casi se mantenga en la posici´on deseada.
Finalmente, se ajusta Ki. Esta componente solo ayuda al robot a alcanzar la posici´on precisa; si las otras dos componentes no se han ajustado correctamente, Ki no cambiar´a radicalmente el comportamiento del robot. En resumen, Kp y Ki son las m´as importantes.

Valores peque˜nos:
Los valores del PID dependen en gran medida de la construcci´on del robot. Es importante tener en cuenta que cuanto mayores sean los valores, m´as agresivo ser´a el movimiento del robot. Se recomienda comenzar con valores menores a 1 y realizar incrementos peque˜nos para evitar que el robot se mueva bruscamente.

### 10. Programaci´on inicial

Al combinar los c´odigos previamente agregados a esta documentaci´on con un control PID, podemos lograr que el robot funcione. Sin embargo, es necesario ajustar los valores del PID para que se adapten a nuestro caso espec´ıfico.

1 | # include " Wire .h"
2 | # include " I2Cdev .h"
3 | # include " MPU6050 .h"

4
5 MPU6050 sensor ;

6
7 | // Definiciones de pines de motores
8 | const int pinPWMA = 16;
9 | const int pinAIN2 = 17;
10 | const int pinAIN1 = 18;
11 | const int pinPWMB = 22;
12 | const int pinBIN1 = 19;
13 | const int pinBIN2 = 21;
14 | const int pinSTBY = 23;

15

16
17 | // Variables del sensor MPU6050
18 | int16_t ax , ay , az ;
19 | int16_t gx , gy , gz ;
20 | long tiempo_prev ;
21 | float dt ;
22 | float ang_x , ang_y ;
23 | float ang_x_prev , ang_y_prev ;

24
25 | // Variables PID
26 | float Kp = 0; // Ajusta estos 3 valores s e g n sea necesario
27 | float Ki = 0;
28 | float Kd = 0;
29 | float integral = 0.0;
30 | float derivative = 0.0;
31 | float previous_error = 0.0;

32
33 | void setup () {
34 | Serial . begin (115200) ;
35 | Wire . begin (32 , 33) ;
36 | sensor . initialize () ;

37
38 | // Configurar pines de motores
39 | pinMode ( pinAIN2 , OUTPUT ) ;
40 | pinMode ( pinAIN1 , OUTPUT ) ;

41 | pinMode ( pinPWMA , OUTPUT ) ;
42 | pinMode ( pinBIN1 , OUTPUT ) ;
43 | pinMode ( pinBIN2 , OUTPUT ) ;
44 | pinMode ( pinPWMB , OUTPUT ) ;
45 | pinMode ( pinSTBY , OUTPUT ) ;
46 | }

47
48 | void loop () {
49 | // Obtener datos del MPU6050
50 | sensor . getAcceleration (& ax , & ay , & az ) ;
51 | sensor . getRotation (& gx , &gy , & gz );

52
53 | // Calcular | ngulos | con el a c e l e r m e t r o
54 | float accel_ang_x = atan ( ay / sqrt ( pow (ax , 2) + pow (az , 2) )) * (180.0 / PI ) ;
55 | float accel_ang_y = atan (- ax / sqrt ( pow ( ay , 2) + pow (az , 2) )) * (180.0 / PI );

56
57 | // Calcular | ngulo | de r o t a c i n con giroscopio y filtro complementario
58 | dt = ( millis () - tiempo_prev ) / 1000.0;
59 | tiempo_prev = millis () ;
60 | ang_x = 0.98 * ( ang_x_prev + ( gx / 131.0) * dt ) + 0.02 * accel_ang_x ;
61 | ang_y = 0.98 * ( ang_y_prev + ( gy / 131.0) * dt ) + 0.02 * accel_ang_y ;

62
63 | ang_x_prev = ang_x ;
64 | ang_y_prev = ang_y ;

65
66 | // Control del p n d u l o invertido usando PID
67 | float desired_angle = 0.0; | // | ngulo | deseado para mantener el equilibrio
68 | float error = desired_angle - ang_x ; | // Calcular error

69
70 | integral += error * dt ;
71 | derivative = ( error - previous_error ) / dt ;

72
73 float motor_speed = Kp * error + Ki * integral + Kd * derivative ;

74
75 | // Controlar los motores
76 | enableMotors () ;
77 | moveMotor ( pinPWMA , pinAIN1 , pinAIN2 , motor_speed );
78 | moveMotor ( pinPWMB , pinBIN1 , pinBIN2 , motor_speed );

79
80 | // Mostrar los | ngulos | y la velocidad de los motores
81 | Serial . print (" Rotacion en X: ") ;
82 | Serial . print ( ang_x );
83 | Serial . print (", Error : ");
84 | Serial . print ( error );
85 | Serial . print (", Velocidad de los motores : ");
86 | Serial . println ( motor_speed );

87
88 | // Actualizar el error anterior
89 | previous_error = error ;

90
91 | delay (1) ; // Reducir el tiempo de espera para aumentar la frecuencia de muestreo
92 | }

93
94 | // Funciones adicionales
95 | void moveMotor ( int pinPWMA , int pinIN1 , int pinIN2 , float speed ) {
96 | if ( speed > 0) {
97 | digitalWrite ( pinIN1 , HIGH );
98 | digitalWrite ( pinIN2 , LOW );
99 | analogWrite ( pinPWMA , speed );
100 | } else {
101 | digitalWrite ( pinIN1 , LOW );
102 | digitalWrite ( pinIN2 , HIGH );
103 | analogWrite ( pinPWMA , - speed );
104 | }
105 | }

106
107 | void enableMotors () {
108 | digitalWrite ( pinSTBY , HIGH );
109 | }
Listing 5: C´odigo inicial completo

### 11. Control con mando

Este apartado a´un est´a por desarrollarse.

## Anexo B. Manual de robot Kobuki/Turtlebot2

Manual de usuario del robot Kobuki/Turtlebot2 para la extracción de parámetros de los motores del robot, para la realización del ejercicio de modelado en el espacio de estados.

EPSE - Campus Terra (Lugo) | 39 / 63 | e.comesana@usc.es

# Kobuki User Guide

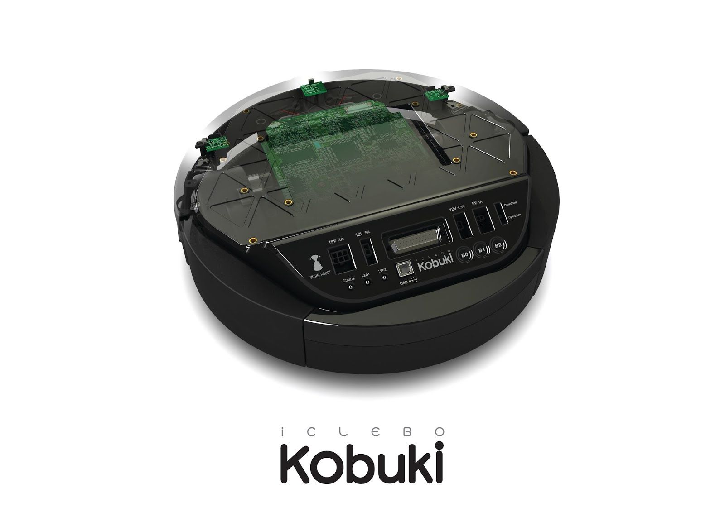
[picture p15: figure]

Version 1.1.0
2017/03/15

## Contents

Contents

About

Basic Usage
Charging
First Run
Software
Problems

Advanced Usage
Replacing Batteries
Updating Firmware
Linux
Windows
Serial Port Connectivity
Adding a Custom Sensor Array

Specifications
Safety Guideline
Functional
Hardware
Software

Anatomy
Top View
Bottom View
Control Panel
Connectors
Models & Drawings
Motors
Gyro
Power Adapter
Batteries
Serial Port

Firmware
Communication
Protocol Specification
Version Checking
Updating
Special Firmware Modes
Activating
Random Walker Mode
Arduino / Embedded Board Support Mode

ChangeLog

License

## About

Introducing Korea’s first robotic turtle.

kobuki [거북이] n. turtle

Kobuki is robotically engineered to be long-lived, tough and fast. With high performance batteries, Kobuki will tirelessly work alongside you through those long coffee-powered nights. He’ll also happily burden himself with your modded array of sensors, actuators, laptops, embedded boards, portside cannons and do it all at a speed that makes his real world cousins seem like … well, turtles.

Use him for serving 치맥 (chi-mek), chasing your neighbour’s kids or simply, to make your own robot ideas become reality.

Kobuki is still young, don’t expect him to remain as he is . Kobuki’s development has already been significantly influenced by the community and as he marches towards old age, we will continue to work with the community and you to ensure he becomes better with time.

Sincerely,
Kobuki Team.

## Basic Usage

Make sure be aware of the safety guidelines.

### Charging

Connect the power adapter to Kobuki or dock Kobuki in the docking station. If Kobuki is turned on, you will hear a short sound when charging starts and the LED will light up appropriately.

- Green : fully charged
- Blinking Green : charging
- Orange : low battery

Tip: the battery still charges if Kobuki is off, but you will not see the LED, nor hear sounds

### First Run

You want to see Kobuki in action without further ado? Kobuki has a special random walker mode embedded into the firmware which you can activate on start-up:

1. Turn on Kobuki.
2. Within the first 3 seconds press the B0 button and hold for 2 seconds.
3. LED2 will start blinking and Kobuki wander around.

Tip: this was introduced to the firmware in v1.1.0. In case your kobuki is not running this or a later version, please refer to the section about updating the firmware.

### Software

In order to gain access to all of Kobuki’ s features, you will need an external computing unit (pc/laptop/tablet/embedded board) with software which communicates with Kobuki. Officially supported systems include:

## Build Your Own Kobuki Driver

Use the Serial Protocol

## Linux C++ Application

Use the Kobuki C++ Driver

## Kobuki for ROS

Use the Kobuki ROS World

Alternatively, you can get started with the Turtlebot 2 Platform which runs on a Kobuki base.

Info: other platforms have had experimental support at one stage or another (windows/arduino/android).

### Problems

Reach out on the following channels:

## Advanced Usage

- Kobuki User’s Mailing List: kobuki-users@yujinrobot.com
- ROS Community Answers: http://answers.ros.org/questions/tags%3Akobuki
- Yujin Sales Support: kobuki@yujinrobot.com

Note: Kobuki comes with a 1 year warranty. In case you bought Kobuki from another one of Yujin Robot’s distributors, please contact them, otherwise email Yujin Sales Support.

### Replacing Batteries

Warning: the electronics does not support the use of multiple battery packs at the same time!

Flip the kobuki | Open the case
Unplug | Swap batteries
Replug | Replace the case

### Updating Firmware

If you have a ROS installation, you can find the current version by running:

$ rosrun kobuki_driver version_info
# Version Info:

* Hardware Version: 1.0.4
* Firmware Version: 1.2.0
* Software Version: 0.7.7
* Unique Device ID: 97713968-842422349-1361404194

Alternatively you can compile version_info.cpp (no ROS) to create your own version checker.

Linux

The Flashing Utility

# Download & build the flashing utility

$ wget http://files.yujinrobot.com/kobuki/firmware/stm32flash-0.4.tar.gz $ tar -xvzf stm32flash.tar.gz
$ cd stm32flash
$ make

Download the Firmware

# choose the firmware version from http://files.yujinrobot.com/kobuki/firmware # e.g. latest

$ wget http://files.yujinrobot.com/kobuki/firmware/kobuki_firmware-latest.hex

Identify the ttyUSBx Port

If you have a udev rule installed, it will show up as /dev/kobuki, but if not, you can typically find it under one of the ttyUSB ports, e.g. /dev/ttyUSB0. If you are not sure, type dmesg into a terminal, unplug and replug the robot and type dmesg again. You should now be able to see which port is assigned to the robot (more precisely the FTDI USB to serial converter).

Switch to Download Mode

1. Connect the robot to your PC using the USB cable
2. Turn off the robot (switch on the side)
3. Switch from normal runtime mode to firmware download mode

This simply changes the type of data that is sent back and forth along the usb connection. You can do this by moving the switch illustrated below into the ‘download’ (up) position. Note that this switch is embedded into the robot cover so it isn’t easily thrown by accident – you may need thin plyers or some similar tool. You can find the mode switch mechanism on the right side of the control panel -see the image below.

Flashing

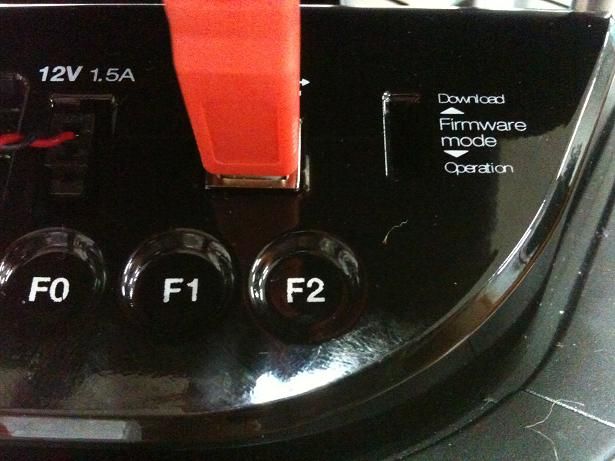
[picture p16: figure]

Note: The following instructions assume flashing of kobuki_firmware-latest.hex and port /dev/ttyUSB0. Modify these if necessary.

Warning: you need to execute the flashing command IMMEDIATELY after turning the robot on!

1. Turn off the robot
2. Check that the switch is in download mode
3. Turn on the robot

$ ./stm32flash -b 115200 -w kobuki_firmware_firmware-latest.hex /dev/ttyUSB0 stm32flash 0.4

http://stm32flash.googlecode.com/

Using Parser : Intel HEX
Interface serial_posix: 115200 8E1
Version | : 0x22
Option 1 | : 0x00
Option 2 | : 0x00
Device ID : 0x0414 (High-density)
- RAM | : 64KiB (512b reserved by bootloader)
- Flash | : 512KiB (sector size: 2x2048)
- Option RAM : 16b
- System RAM : 2KiB
Write to memory
Erasing memory
Wrote address 0x0800a3f0 (100.00%) Done.

Rebooting

- Turn off the robot power
- Flick the firmware switch back to ‘Operation’ mode.
- Turn on the robot power
- I’m happy, you should be too!

Windows

The Flashing Utility

- Download and install the windows flashing utility

Download the Firmware

Find and download the version of the firmware you wish to flash from the Kobuki FW File Server.

Identify the COM Port

Usually if this will show up on COM1, but check to make sure.

Switch to Download Mode

1. Connect the robot to your PC using the USB cable
2. Turn off the robot (switch on the side)
3. Switch from normal runtime mode to firmware download mode

This simply changes the type of data that is sent back and forth along the usb connection. You can do this by moving the switch illustrated below into the ‘download’ (up) position. Note that this switch is embedded into the robot cover so it isn’t easily thrown by accident – you may need thin plyers or some similar tool. You can find the mode switch mechanism on the right side of the control panel -see the image below.

Flashing

1. Turn off the robot
2. Check that the switch is in download mode
3. Turn on the robot

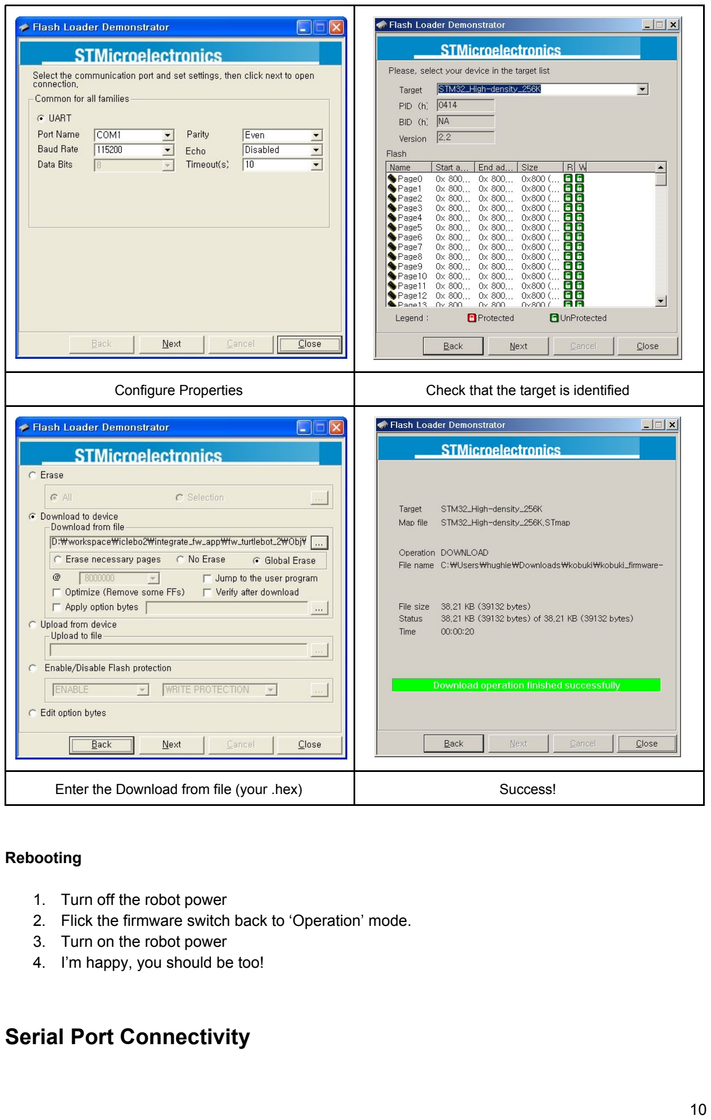
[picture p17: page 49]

Configure Properties | Check that the target is identified
Enter the Download from file (your .hex) | Success!

Rebooting

1. Turn off the robot power
2. Flick the firmware switch back to ‘Operation’ mode.
3. Turn on the robot power
4. I’m happy, you should be too!

### Serial Port Connectivity

Many embedded boards do not have usb interfaces, or the embedded board doesn’t have the necessary ftdi32 serial->usb support. In these cases it is simpler to utilise the serial port on Kobuki’s expansion port to driving kobuki by serial interface instead of USB.

Pinouts

Pictured below are the pinouts of Kobuki’s expansion port, include the serial pins. The minimum number of required pins for serial communication is three; TX, RX, and GND. Additionally EX3.3 or EX5 can be used for powering external devices, such as line transceiver.

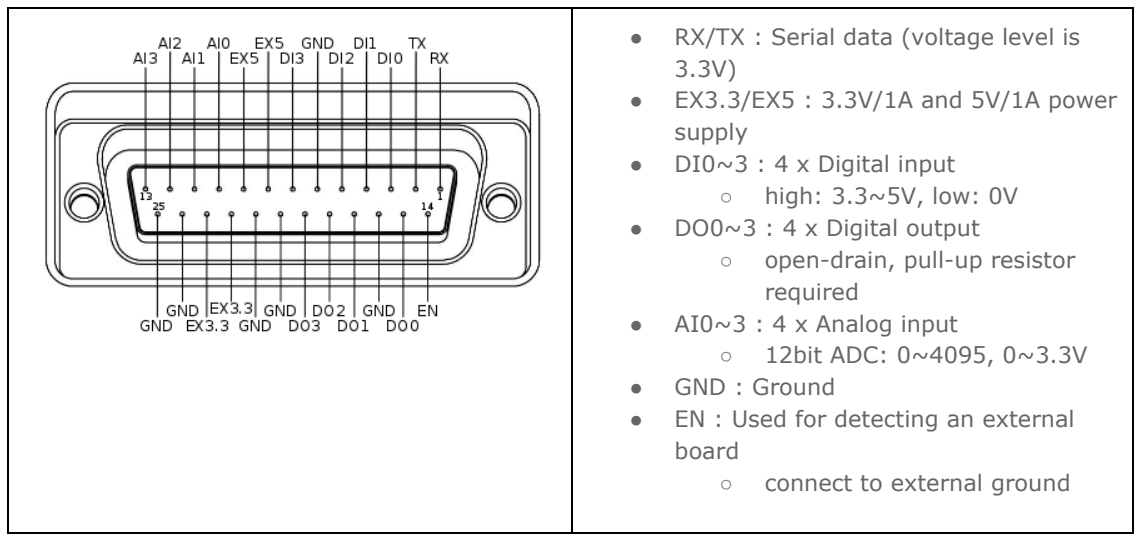
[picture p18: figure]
● RX/TX : Serial data (voltage level is 3.3V) ● EX3.3/EX5 : 3.3V/1A and 5V/1A power supply ● DI0~3 : 4 x Digital input ○ high: 3.3~5V, low: 0V ● DO0~3 : 4 x Digital output ○ open-drain, pull-up resistor required ● AI0~3 : 4 x Analog input ○ 12bit ADC: 0~4095, 0~3.3V ● GND : Ground ● EN : Used for detecting an external board ○ connect to external ground

Connections

a) RS-232 Interface

The voltage level of serial port is 3.3V. To connect kobuki with the standard RS-232 serial port, you should use line transceiver in the middle to convert voltage level. MAX232 chip is typical solution for it. Below diagram show simplified typical example of connections between Kobuki and SBC (your embedded board, laptop or pc). EX3.3 pin is used to powering line transceiver. It can be EV5 pin or external power sources from outside.

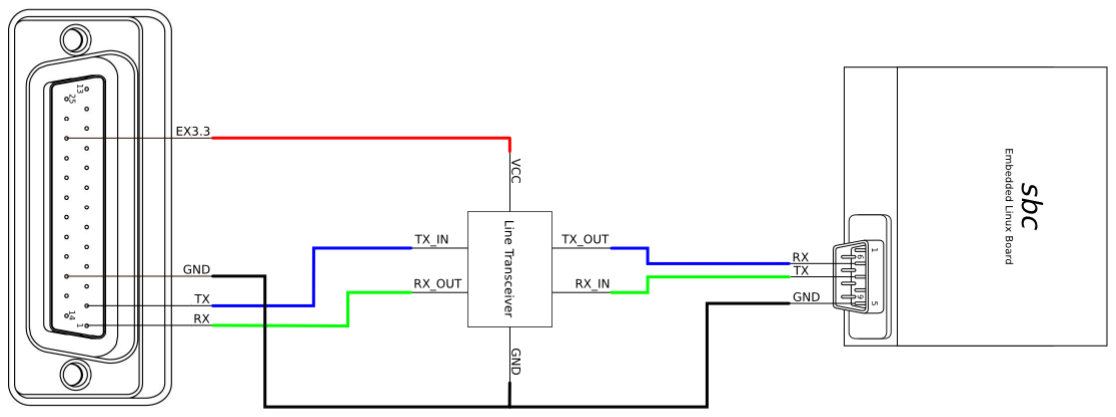
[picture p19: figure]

b) Logic Level Interface

To connect kobuki with serial port of MCU directly, below is the simplest connection diagram can be used. Serial pins of kobuki are 5V-tolerant. It accepts 3.3V and 5V voltage levels typically used by integrated circuit. Connection with power pin(EX3.3 or EX5) is optional, if you powering MCU with independent sources, such as battery, or wall adaptor.

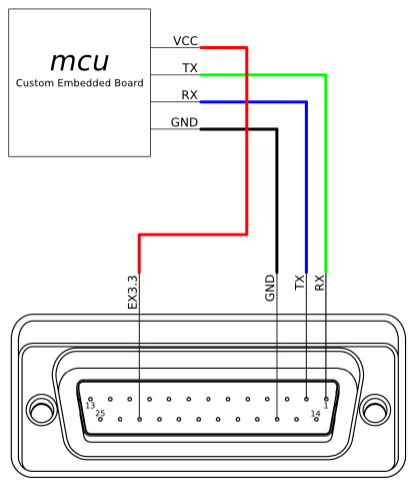
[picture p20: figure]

Building An Application

If you’re using the ROS implementation, or building atop the kobuki c++ driver, simply re-configure the port string used for the application and everything should be ready to go.

If building an experimental driver from scratch (e.g. android driver), then you will need to implement the Kobuki Protocol specification.

### Adding a Custom Sensor Array

Kobuki usually gets equipped with a 3d sensor These typically have limitations as obstacle avoidance sensor:

- Narrow fov (58° x 43° horizontal x vertical)
- Death zone on the first 45 cm
- Cannot detect glass walls
- Cannot detect polished metallic surfaces

In one experiment an 11 IR sensors half ring, pointing 12 degrees downward was added to compensate.

- Sensor model: Sharp GP2Y0A21YK
- Power supply: Kobuki’s 5V, 1A
- Sensor reading: Arduino MEGA 2560
- PC interface: Arduino custom firmware – Bosch adc_driver
- Mounting: 3D printed frame.

The analog output of sensors is read by the Arduino board, while for power and ground they are connected to Kobuki’s 5V 1A power source. Connecting several sensors to the same power supply makes readings very noisy when there aren’t obstacles. The solution was to put decoupling capacitors on each sensor. For interfacing Arduino, we use Bosch adc_driver. A funny problem comes sometimes when looking at corners in a particular angle (~30 degrees) : sensors get a spurious reading, no idea why. We just went on with this, as is not a common problem.
Different mounting frames are available for downloading and printing in our file server:
- Horizontally mounted MaxBotix’s LV-Maxsonars
- Horizontally mounted Sharp IR sensors
- 12 degrees downward pointing Sharp IR sensors

And the result:

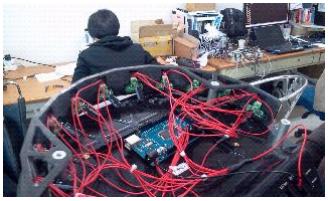
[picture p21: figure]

## Specifications

### Safety Guideline

- Do not twist or subject the power cable to extreme pressure or weight weight.
- Keep the pin and interface of the power plug clean from dust or water.
- Do not pull the power cord or touch the power plug with wet hands.
- Do not use with a damaged power plug, power cord or loose outlet.
- Use Kobuki indoors only.
- Do not pour or spray water onto Kobuki.
- Do not use Kobuki to pick up anything that is burning or smoking.
- Always remove the battery before long-term storage or transportation.

### Functional

- Maximum translational velocity: 70 cm/s

- Maximum rotational velocity: 180 deg/s (>110 deg/s gyro performance will degrade)
- Payload: 5 kg (hard floor), 4 kg (carpet)
- Cliff: will not drive off a cliff with a depth greater than 5cm
- Threshold Climbing: climbs thresholds of 12 mm or lower
- Rug Climbing: climbs rugs of 12 mm or lower
- Expected Operating Time: 3/7 hours (small/large battery)
- Expected Charging Time: 1.5/2.6 hours (small/large battery)
- Docking: within a 2mx5m area in front of the docking station

### Hardware

- PC Connection: USB or via RX/TX pins on the parallel port
- Motor Overload Detection: disables power on detecting high current (>3A)
- Odometry: 52 ticks/enc rev, 2578.33 ticks/wheel rev, 11.7 ticks/mm
- Gyro: factory calibrated, 1 axis (110 deg/s)
- Bumpers: left, center, right
- Cliff sensors: left, center, right
- Wheel drop sensor: left, right
- Power connectors: 5V/1A, 12V/1.5A, 12V/5A
- Expansion pins: 3.3V/1A, 5V/1A, 4 x analog in, 4 x digital in, 4 x digital out
- Audio : several programmable beep sequences
- Programmable LED: 2 x two-coloured LED
- State LED: 1 x two coloured LED [Green - high, Orange - low, Green & Blinking - charging]
- Buttons: 3 x touch buttons
- Battery: Lithium-Ion, 14.8V, 2200 mAh (4S1P - small), 4400 mAh (4S2P - large)
- Firmware upgradeable: via usb
- Sensor Data Rate: 50Hz
- Recharging Adapter: Input: 100-240V AC, 50/60Hz, 1.5A max; Output: 19V DC, 3.16A
- Netbook recharging connector (only enabled when robot is recharging): 19V/2.1A DC
- Docking IR Receiver: left, centre, right

### Software

- C++ drivers for Linux
- ROS driver
- Gazebo simulation

## Anatomy

### Top View

### Bottom View

### Control Panel

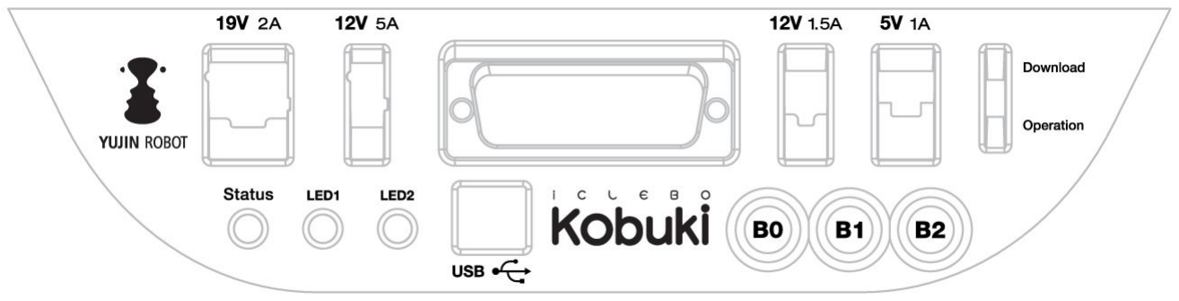
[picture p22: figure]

- 19V/2A: Laptop power supply
- 12V/5A: Arm power supply
- 12v/1.5A: Microsoft Kinect power supply
- 5V/1A: General power supply
- Status LED: Indicates Kobuki’s status
- Green: Kobuki is turned on and battery at high voltage level
- Orange: On - Low battery voltage level (please charge soon)
- Green blinking: On - Battery charging
- Off: Kobuki is turned off.
- LED1/2: Programmable LEDs
- USB: Data connection
- BO/1/2: Buttons
- Firmware switch: Enable/disables the firmware update mode

### Connectors

SOME NOTES ABOUT THE MOLEX PAGES BELOW

1. We do not actually use Molex connectors but we are supplied by a Korean vendor who produces connectors according to the Molex standard. These links will be more useful to internationals in helping them find a mating part that works for them.
2. The images on each page are representative of the series of connectors. Each series usually has a variety of connectors with a different number of pins. As a result, the pictures on some of the pages below may seem as though they have the incorrect number of pins, but do not worry about this – they are the correct links. Note that you can jump to different connectors in the series via the second part of their identification number (e.g. 43045-0224 for the 2-pin, 43045-0424 for the 4-pin).
3. If some linked connectors are listed as obsolete on the molex website, don’t worry. The connector you are exactly requiring are those you can find under the ‘Mates with Parts’ link on each page. If these however should become obsolete as well, please let us know via email.

Power

- 5V@1A Molex PN : 43650-0218 – for custom boards
- 12V@1.5A : Molex PN : 43045-0224 – specially supporting the kinect
- 12V@5A : Molex PN : 3929-9023 – for high powered accessories (e.g. robotic arm)
- 19V@2A : Molex PN : 3928-9068 – for recharging netbooks

Battery

- 4S1P/4S2P Battery Pack Connector

I/O Port

- DB25 pin D-SUB Female connector that provides the following functionality (pdf)

Cables

Note, if you click on the preceding links for the power connectors, under the heading ‘Mates with Part(s)’ you can find the compatible connector to use with each power source. The most important one being of course:

- 12V@1.5A : Molex PN : 43025-0200 – specially supporting the kinect

### Models & Drawings

The models and drawings include both the base and parts for the Turtlebot 2.

- 2D mechanical drawings – DWG, PDF
- 3D models – IGS, STEP

The inserts in the kobuki plate are M4 threads (metric, 4mm). If you wish to build standoffs compatible for these inserts, please reference the pole pdf’s in the 2D mechanical drawings which are what we use for turtlebots.

### Motors

Specifications

- Brushed DC Motor
- Motor Manufacturer: Standard Motor
- Part Name: RP385-ST-2060
- Rated Voltage: 12 V
- Rated Load: 5 mN·m
- No Load Current: 210 mA
- No Load Speed: 9960 rpm ± 15%
- Rated Load Current: 750 mA
- Rated Load Speed: 8800 rpm ± 15%
- Armature Resistance: 1.5506 Ω at 25°C
- Armature Inductance: 1.51 mH
- Torque Constant(Kt): 10.913 mN·m/A

- Velocity Constant(Kv): 830 rpm/V
- Stall Current: 6.1 A
- Stall Torque: 33 mN·m

Control Method

- Driven by voltage source(H-bridge)
- Controlled by Pulse-width modulation(PWM)

### Gyro

Specification

- 3-Axis Digital Gyroscope
- Manufacturer : STMicroelectronics
- Part Name : L3G4200D
- Measurement Range: ±250 deg/s
- Yaw axis is factory calibrated within the range of ±20 deg/s to ±100 deg/s

Performance

In-Place Rotation Test

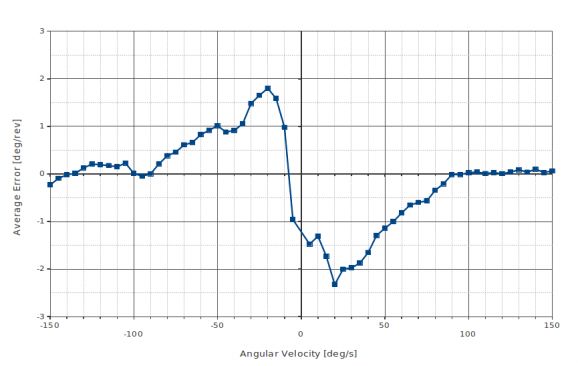
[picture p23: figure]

This graph shows the average heading error per revolution of gyro, when robot rotates with a given velocity.

Square Path Test

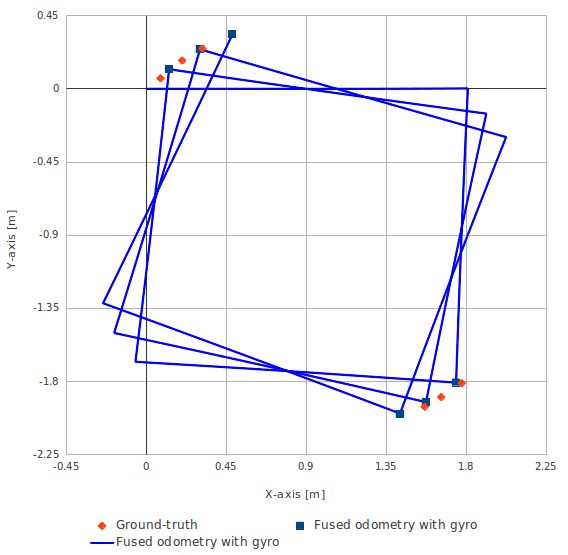
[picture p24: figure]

This graph shows the position error of fused odometry with gyro, when robot moves along a square path. Robot moved with 0.1 m/s on the line segment and rotated with 30 deg/s on the corner.

Number of turns of square path | Angular Error [deg]
0.5 | 0.47
1.5 | 1.99
2.5 | 3.18

This table shows the calculated angular error, when robot arrived at the diagonally opposite corner from the starting point (0.0, 0.0).

### Power Adapter

Input

- Voltage: 100-240V
- Frequency: 50/60Hz
- Ampere: 1.5A Max

Output

- Voltage: 19V
- Ampere: 3.16A

Other

- Photo
- Specification 1
- Specification 2

### Batteries

Kobuki by the default ships with a small Lithium-Ion battery pack (4S1P, 2200mAh, 14.8V).

Tip: for extra long operation, a big battery pack (4S2P, 4400mAh, 14,8V) can be ordered as well.

Warning: the electronics does not support the use of multiple battery packs at the same time (even if there is room in the battery compartment)

Specifications

- Data Sheet (pdf)

Pinouts

- Red: battery (+), 9.6 V ~ 16.8 V
- White: NTC thermistor to ground, 10 kΩ ± 1%
- Black: battery(-), Ground

Charging Profile

This plot shows the voltages as measured by the robot’s hardware. Both the standard 4S1P and the extra 4S2P batteries are compared. During the test, the robot was charging via adaptor.

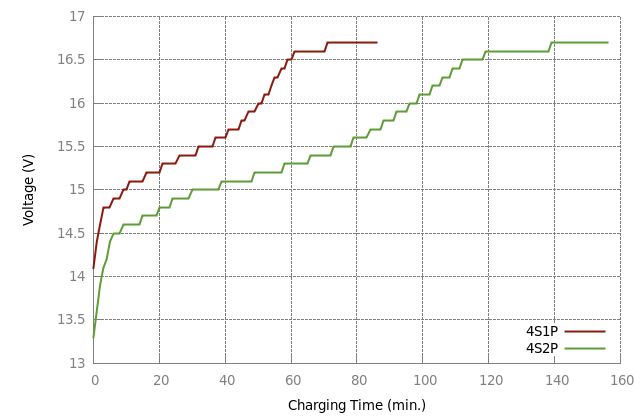
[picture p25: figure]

Discharging Profile

This plot shows the voltage as measured by the robot’s hardware. Both the standard 4S1P and the extra 4S2P batteries are compared. During the test, the robot was continuously spinning, with the Kinect camera running.

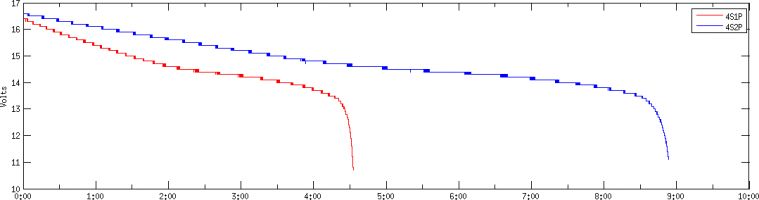
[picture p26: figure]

### Serial Port

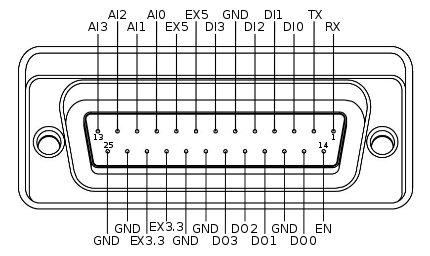
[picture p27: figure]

- RX / TX: Serial data connection (RS232; used voltage level is 3.3V!)
- EX3.3 / EX5: 3.3V/1A and 5V/1A power supply
- DI0 - 3: 4 x Digital input (high: 3.3 - 5V, low: 0V)
- DO0 - 3: 4 x Digital output (open-drain, pull-up resistor required)
- AI0-3: 4 x Analog input (12bit ADC: 0 - 4095, 0 - 3.3V)
- GND: Ground
- EN: Used for detecting an external board (connect to external ground)

## Firmware

### Communication

- Baud rate: 115200 BPS, Data bit: 8 bit, Stop bit: 1 bit, No Parity
- Electronic protocol: USB / RS232 (@ DB25 connector)

### Protocol Specification

The driver communicates with the robot by using predefined protocol. In general, the driver sends the commands to the robot and the robot sends some feedback data or sensor readings. This command and feedback data are converted into bytestreams for communication via serial interface. The protocol specify that rules and forms of bytestream.

For more detailed information, visit:
- http://yujinrobot.github.com/kobuki/enAppendixProtocolSpecification.html

### Version Checking

Every time the robot comes alive (because it is connected or powered on), the driver checks the compatibility between software (i.e. driver) and firmware. Firmware versions are of the form M.m.p, where:

- M(ajor) represents a deep rebuild of the code that almost surely breaks protocol compatibility. In consequence, if mayor version doesn’t match, the driver will show an error, suggest the required update and shutdown.
- m(inor) represents a new feature that could not work if the driver is outdated, but the protocol itself is spared. In consequence, if minor version doesn’t match, the driver will show a warning suggesting the required update and continue working.
- p(atch) represents a fix on the code and is not checked at all.

You can check which firmware version your robot is running on the log (check the first lines on stdout at driver startup), by running the version_info program included on the kobuki driver, or if you are using ROS, just echoing /mobile_base/version_info topic. Generally speaking, it’s recommended to upgrade the firmware to the latest stable version.

### Special Firmware Modes

Activating

Kobuki has some special firmware modes, which can be activated on startup. Currently implemented are:
I. Random walker mode
II. Arduino/Embedded board support mode

To activate one of them, follow these instructions:
1. Turn on Kobuki.

2. Within in the first 3 seconds press and hold button BO(I) / B1 (II) for 2 seconds.
3. If* you see LED2(I) / LED1(II) switching between red and green, your chosen mode is activated.

Note(*): These modes have been introduced to the firmware with version 1.1.0. In case your Kobuki is not running this or a later version, please refer to the section about updating the firmware.

Random Walker Mode

In the random walker mode Kobuki is driving around until it hits an object with the bumper or a cliff is detected. In both cases, Kobuki will stop, turn by a random amount of degrees and continue driving .

Note: In this mode Kobuki’s wheel drop sensors are not activated. So, be careful when lifting up Kobuki!

Arduino / Embedded Board Support Mode

In this mode the serial port (DB25 connector) gives access to basic controls of Kobuki. You can hook up the digital/analog inputs/outpus of your Arduino or other embedded boards and start writing simple control programs.

Below is the special pin setting listed. Please refer to the serial port description for the name to pin mapping.

- DI0: Not used
- DI1: Not used
- DI2: Not used
- DI3: Not used
- DO0: Bumper left (pressed/released)
- DO1: Bumper centre (pressed/released)
- DO2: Bumper right (pressed/released)
- DO3: Wheel drop sensors (at least one wheel is dropped / none is dropped)
- AI0: Wheel speed right (0V - full speed backward, 3.3V - full speed forward)
- AI1: Wheel speed left (0V - full speed backward, 3.3V - full speed forward)
- AI2: Not used
- AI3: Not used

All other pins (GND, RX, TX etc.) remain unchanged.

Note: To enable the motors you need to press button B0.

## Resources

- Kobuki Images & Renderings
- Turtlebot Images & Renderings
- Marketing Materials

## ChangeLog

- 1.0.0 : official release
- 1.0.1 : upgrading firmware link fix
- 1.0.2 : documentation link fix
- 1.0.4 : updating the spec. of serial communication
- 1.0.5 : fixing battey & connector link
- 1.0.6 : updating link after Kobuki web site revision
- 1.1.0 : reorganised and collapsed website howtos into the guide

## License

The Kobuki user guide is licensed under a Creative Commons Attribution-ShareAlike 3.0 Unported License.

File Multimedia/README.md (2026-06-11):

En esta carpeta se incluyen las fotos y videos del robot.

La estructura de la carpeta es la siguiente:

- `README.md/`: Este fichero.
  
- Fotos:
  - `IMG_3162.jpeg/`
  - `IMG_3164.jpeg/`
  - `IMG_3166.jpeg/`
    
- Videos:
  - `video1/`
  - `video2/`
  - `video3/`

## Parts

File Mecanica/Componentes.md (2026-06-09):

| Componente | Cantidad | Precio | Enlace |
|---|---|---|---|
| Motores | 2 | 2,5 € |[Electrocomponentes](https://www.electrocomponentes.es/motores-y-servos/1556-motor-3-6v-con-reductora-y-rueda-100rpm-200rpm-481-para-robot-smart-car.html) |
| Chasis | 1 | 0 € | Impresoras de la universidad |
| Cables | 2 (m) | 0.45 € (Por metro) | [Electrocomponentes](https://www.electrocomponentes.es/8-cable) |
| Interruptor | 1 | 8,99 € | [Amazon](https://www.amazon.es/dp/B07ZTJNRXT?ref=ppx_yo2ov_dt_b_fed_asin_title) |
| Tornillos métrica Ø 3 x L.35 mm | 4 | 0 € | |
| Tuerca métrica Ø 3 mm | 4 | 0 € | |

Aquellos que no tienen enlace es porque son componentes que no se compraron y no se recuerda de donde son.

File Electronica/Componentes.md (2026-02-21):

| Componente | Cantidad | Precio | Enlace |
|---|---|---|---|
| PCB | 1 | € |[JLCPCB](https://jlcpcb.com/) |

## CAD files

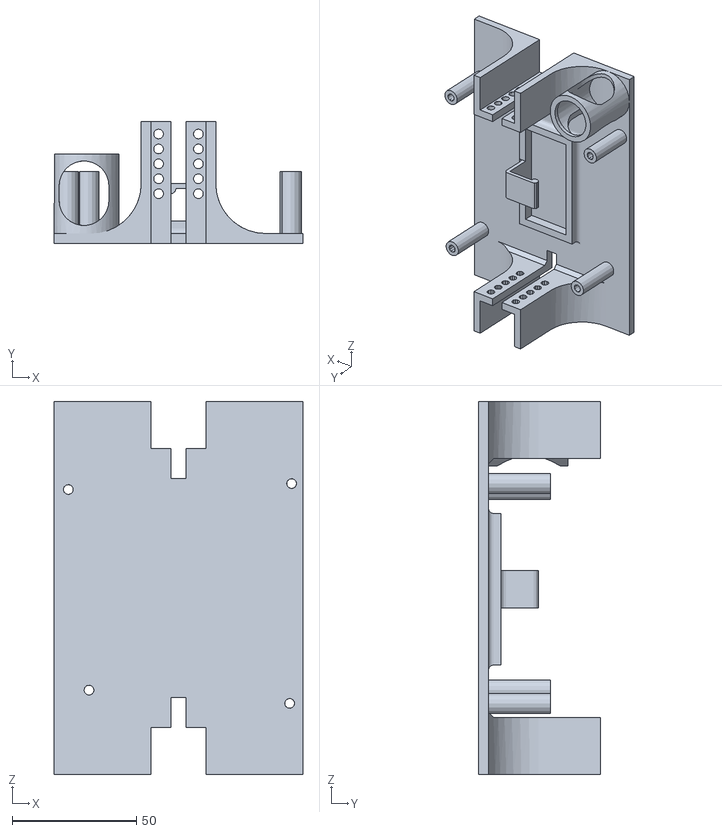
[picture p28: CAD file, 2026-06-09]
Mecanica/CHASIS_V2.stl
100.0 x 49.0 x 150.0

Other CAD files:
Mecanica/CHASIS.ipt

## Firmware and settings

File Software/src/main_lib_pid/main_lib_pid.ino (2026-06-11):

/*
 * main_lib_pid.ino - Prueba de los tres modos PID en el péndulo invertido
 * Comandos por Serial (115200):
 *   S -> MODE_STANDARD (PID clásico)
 *   D -> MODE_DISCRETE (forma de velocidad)
 *   F -> MODE_FILTERED (con filtro en derivada)
 */

#include "Wire.h"
#include "I2Cdev.h"
#include "MPU6050.h"
#include <PIDControl.h>

// Pines de motores
const int pinPWMA = 12, pinAIN1 = 25, pinAIN2 = 33;
const int pinPWMB = 15, pinBIN1 = 26, pinBIN2 = 27;

// PWM máximo permitido (6V motores, 9V batería)
const int PWM_MAX = 170;

// DEADBAND para evitar vibraciones
const int DEADBAND = 25;

// Ángulo de equilibrio y límite de caída
const float EQUILIBRIUM_ANGLE = 0.0f;
const float FALL_ANGLE = 24.0f;

// Filtro complementario
const float ALPHA_COMP = 0.98f;

// Período de muestreo
const double DT_S = 0.01;

// Ganancias PID
const double KP = 18.5;
const double KI = 0.03;
const double KD = 1.5;

// Controladores PID para los tres modos
PIDControl pidS(KP, KI, KD, DT_S, 0.0, MODE_STANDARD);
PIDControl pidD(KP, KI, KD, DT_S, 0.0, MODE_DISCRETE);
PIDControl pidF(KP, KI, KD, DT_S, 0.0, MODE_FILTERED);
PIDControl* activePid = &pidF;
PIDMode currentMode = MODE_FILTERED;

// Sensor MPU6050
MPU6050 sensor;
int16_t ax, ay, az, gx, gy, gz;
float gy_offset = 0.0f;
float ang_y = 0.0f, ang_y_prev = 0.0f;

// Prototipos de funciones
void moveMotor(int pwmPin, int in1, int in2, float speed);
void switchMode(PIDMode mode, const char* name);


// ═══════════════════════════════════════════════════════════════════════════════
void setup() {
    Serial.begin(115200);
    Wire.begin(18, 19);
    Wire.setClock(400000);
    sensor.initialize();

    // Calibración del MPU6050
    sensor.setXAccelOffset(-736);
    sensor.setYAccelOffset(1299);
    sensor.setZAccelOffset(1522);
    sensor.setXGyroOffset(166);
    sensor.setYGyroOffset(250);
    sensor.setZGyroOffset(56);

    if (!sensor.testConnection()) {
        Serial.println("ERROR: MPU6050 no detectado. Revisa el cableado I2C.");
        while (true) delay(100);
    }

    // Configurar pines de motores
    const int motorPins[] = {pinAIN1, pinAIN2, pinPWMA, pinBIN1, pinBIN2, pinPWMB};
    for (int i = 0; i < 6; i++) {
        pinMode(motorPins[i], OUTPUT);
    }

    moveMotor(pinPWMA, pinAIN1, pinAIN2, 0);
    moveMotor(pinPWMB, pinBIN1, pinBIN2, 0);

    // Configurar setpoint y límites
    pidS.establecerSetpoint(EQUILIBRIUM_ANGLE);
    pidS.establecerLimiteSalida(-PWM_MAX, PWM_MAX);
    pidD.establecerSetpoint(EQUILIBRIUM_ANGLE);
    pidD.establecerLimiteSalida(-PWM_MAX, PWM_MAX);
    pidF.establecerSetpoint(EQUILIBRIUM_ANGLE);
    pidF.establecerLimiteSalida(-PWM_MAX, PWM_MAX);

    // Ángulo inicial
    sensor.getAcceleration(&ax, &ay, &az);
    ang_y = atan2f(-(float)ax, sqrtf((float)ay*(float)ay + (float)az*(float)az)) * (180.0f / PI);
    ang_y_prev = ang_y;

    Serial.println("PIDControl - Pendulo Invertido");
    Serial.printf("KP=%.2f KI=%.2f KD=%.2f DT=%dms\n",
                  (float)KP, (float)KI, (float)KD, (int)(DT_S * 1000));
    Serial.println("Comandos: S=STANDARD D=DISCRETE F=FILTERED");
}


// ═══════════════════════════════════════════════════════════════════════════════
void loop() {
    unsigned long t0 = millis();

    // Comandos por Serial
    if (Serial.available()) {
        char command = (char)toupper(Serial.read());
        if (command == 'S') {
            switchMode(MODE_STANDARD, "STANDARD");
        } else if (command == 'D') {
            switchMode(MODE_DISCRETE, "DISCRETE");
        } else if (command == 'F') {
            switchMode(MODE_FILTERED, "FILTERED");
        }
    }

    // Leer sensor
    sensor.getAcceleration(&ax, &ay, &az);
    sensor.getRotation(&gx, &gy, &gz);

    // Calcular ángulo desde acelerómetro
    float accel_ang = atan2f(-(float)ax, sqrtf((float)ay*(float)ay + (float)az*(float)az)) * (180.0f / PI);

    // Velocidad angular
    float gy_dps = ((float)gy - gy_offset) / 131.0f;

    // Filtro complementario
    ang_y = ALPHA_COMP * (ang_y_prev + gy_dps * (float)DT_S) + (1.0f - ALPHA_COMP) * accel_ang;
    ang_y_prev = ang_y;

    float error = EQUILIBRIUM_ANGLE - ang_y;

    // Protección por caída
    if (fabsf(error) > FALL_ANGLE) {
        moveMotor(pinPWMA, pinAIN1, pinAIN2, 0);
        moveMotor(pinPWMB, pinBIN1, pinBIN2, 0);
        pidS.reiniciar();
        pidD.reiniciar();
        pidF.reiniciar();
        return;
    }

    // Calcular salida PID
    float output = (float)activePid->calcular((double)ang_y);

    moveMotor(pinPWMA, pinAIN1, pinAIN2, output);
    moveMotor(pinPWMB, pinBIN1, pinBIN2, -output);

    // Telemetría
    static unsigned long lastPrint = 0;
    unsigned long now = millis();
    if (now - lastPrint >= 50) {
        lastPrint = now;
        const char* modeStr;
        if (currentMode == MODE_STANDARD) {
            modeStr = "STD";
        } else if (currentMode == MODE_DISCRETE) {
            modeStr = "DIS";
        } else {
            modeStr = "FIL";
        }
        Serial.printf("[%s] ang=%6.2f err=%6.2f out=%5.0f\n", modeStr, ang_y, error, output);
    }

    // Sincronizar a DT fijo
    long elapsed = (long)(millis() - t0);
    if (elapsed < 10) {
        delay(10 - elapsed);
    }
}


void switchMode(PIDMode mode, const char* name) {
    pidS.reiniciar();
    pidD.reiniciar();
    pidF.reiniciar();
    currentMode = mode;

    if (mode == MODE_STANDARD) {
        activePid = &pidS;
    } else if (mode == MODE_DISCRETE) {
        activePid = &pidD;
    } else {
        activePid = &pidF;
    }
    Serial.printf("Modo: %s\n", name);
}


void moveMotor(int pwmPin, int in1, int in2, float speed) {
    int pwm = (int)fabsf(speed);

    if (pwm > PWM_MAX) {
        pwm = PWM_MAX;
    }

        if (pwm < DEADBAND) {           
        digitalWrite(in1, LOW);
        digitalWrite(in2, LOW);
        analogWrite(pwmPin, 0);
        return;
    }

    if (speed > 0.0f) {
        digitalWrite(in1, HIGH);
        digitalWrite(in2, LOW);
    } else {
        digitalWrite(in1, LOW);
        digitalWrite(in2, HIGH);
    }

    analogWrite(pwmPin, pwm);
}

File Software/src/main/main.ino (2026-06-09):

#include "Wire.h"
#include "I2Cdev.h"
#include "MPU6050.h"

MPU6050 sensor;

// Pines de motores
const int pinPWMA = 12;
const int pinAIN2 = 33;
const int pinAIN1 = 25;
const int pinPWMB = 15;
const int pinBIN1 = 26;
const int pinBIN2 = 27;

// PWM máximo permitido
const int PWM_MAX = 170;

// Ganancias PID
float Kp = 35.0f;
float Ki = 0.1f;
float Kd = 5.0f;

// Setpoint
float desired_angle = 0.0f;

// Control integral
float integral = 0.0f;
const float INTEGRAL_MAX = 300.0f;

// Límite de caída
const float ANGULO_CAIDA = 24.0f;

// Lecturas del sensor
int16_t ax, ay, az;
int16_t gx, gy, gz;

// Filtro complementario
const float ALPHA = 0.98f;
float ang_y = 0.0f;
float ang_y_prev = 0.0f;
float ang_x = 0.0f;

// Tiempo
unsigned long tiempo_prev = 0;
float dt = 0.0f;
unsigned long ultimo_print = 0;

// Prototipos
void moveMotor(int pinPWM, int pinIN1, int pinIN2, float speed);
void pararMotores();


void setup() {
    Serial.begin(115200);
    Wire.begin(18, 19);
    Wire.setClock(400000);
    sensor.initialize();

    // Calibración del MPU6050
    sensor.setXAccelOffset(-736);
    sensor.setYAccelOffset(1299);
    sensor.setZAccelOffset(1522);
    sensor.setXGyroOffset(166);
    sensor.setYGyroOffset(250);
    sensor.setZGyroOffset(56);

    // Configurar pines
    pinMode(pinAIN2, OUTPUT);
    pinMode(pinAIN1, OUTPUT);
    pinMode(pinPWMA, OUTPUT);
    pinMode(pinBIN1, OUTPUT);
    pinMode(pinBIN2, OUTPUT);
    pinMode(pinPWMB, OUTPUT);
    pararMotores();

    if (!sensor.testConnection()) {
        Serial.println("ERROR: MPU6050 no detectado");
        while (true) {
            delay(1000);
        }
    }

    // Ángulo inicial
    sensor.getAcceleration(&ax, &ay, &az);
    float ang_y_init = atan2(-ax, sqrt((long)ay * ay + (long)az * az)) * (180.0f / PI);
    ang_y = ang_y_init;
    ang_y_prev = ang_y_init;

    tiempo_prev = millis();

    Serial.println("PID control - Pendulo invertido");
    Serial.print("Kp=");
    Serial.print(Kp);
    Serial.print(" Ki=");
    Serial.print(Ki);
    Serial.print(" Kd=");
    Serial.println(Kd);
}


void loop() {
    sensor.getAcceleration(&ax, &ay, &az);
    sensor.getRotation(&gx, &gy, &gz);

    unsigned long ahora = millis();
    dt = (ahora - tiempo_prev) / 1000.0f;
    if (dt <= 0.0f) dt = 0.001f;
    tiempo_prev = ahora;

    float gy_dps = gy / 131.0f;

    // Ángulo desde acelerómetro
    float accel_ang_y = atan2(-ax, sqrt((long)ay * ay + (long)az * az)) * (180.0f / PI);

    // Filtro complementario
    ang_y = ALPHA * (ang_y_prev + gy_dps * dt) + (1.0f - ALPHA) * accel_ang_y;
    ang_y_prev = ang_y;

    ang_x = atan2(ay, sqrt((long)ax * ax + (long)az * az)) * (180.0f / PI);

    float error = desired_angle - ang_y;

    // Protección por caída
    if (fabs(error) > ANGULO_CAIDA) {
        pararMotores();
        integral = 0.0f;
        return;
    }

    // Integral con anti-windup
    integral += error * dt;
    if (integral > INTEGRAL_MAX) integral = INTEGRAL_MAX;
    if (integral < -INTEGRAL_MAX) integral = -INTEGRAL_MAX;

    float P = Kp * error;
    float I = Ki * integral;
    float D = Kd * (-gy_dps);

    float salida = P + I + D;

    if (salida > PWM_MAX) salida = PWM_MAX;
    if (salida < -PWM_MAX) salida = -PWM_MAX;

    moveMotor(pinPWMA, pinAIN1, pinAIN2, salida);
    moveMotor(pinPWMB, pinBIN1, pinBIN2, -salida);

    // Telemetría
    if (millis() - ultimo_print > 50) {
        ultimo_print = millis();
        Serial.print("ang_Y: ");
        Serial.print(ang_y, 2);
        Serial.print("  err: ");
        Serial.print(error, 2);
        Serial.print("  P: ");
        Serial.print(P, 1);
        Serial.print("  I: ");
        Serial.print(I, 1);
        Serial.print("  D: ");
        Serial.print(D, 1);
        Serial.print("  PWM: ");
        Serial.println(salida, 0);
    }
}

void moveMotor(int pinPWM, int pinIN1, int pinIN2, float speed) {
    int pwm = (int)fabs(speed);

    if (pwm > PWM_MAX) {
        pwm = PWM_MAX;
    }

    if (pwm == 0) {
        digitalWrite(pinIN1, LOW);
        digitalWrite(pinIN2, LOW);
        analogWrite(pinPWM, 0);
        return;
    }

    if (speed > 0) {
        digitalWrite(pinIN1, HIGH);
        digitalWrite(pinIN2, LOW);
    } else {
        digitalWrite(pinIN1, LOW);
        digitalWrite(pinIN2, HIGH);
    }
    analogWrite(pinPWM, pwm);
}

void pararMotores() {
    digitalWrite(pinAIN1, LOW);
    digitalWrite(pinAIN2, LOW);
    digitalWrite(pinBIN1, LOW);
    digitalWrite(pinBIN2, LOW);
    analogWrite(pinPWMA, 0);
    analogWrite(pinPWMB, 0);
}

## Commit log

2026-02-21 Fix markdown link formatting for motors
2026-02-22 Agrego la carpeta PCB.zip
2026-02-22 Enhance README with electronic design details
    Added detailed information about the electronic design of the self-balancing robot, including specifications, PCB adaptations, functional schematics, protection measures, and testing procedures.
2026-02-22 Expand README with additional project sections
    Added sections for related projects, hardware setup, chassis design, assembly, component testing, software implementation, and PID tuning.
2026-06-08 Añadiendo archivos de implementación y pruebas para PID y MPU6050
2026-06-08 el main con la libreria PIDControl
2026-06-08 Diseño en inventor del chasis, archivo stl y gcode
    [CHASIS.ipt, CHASIS_V2.stl]
2026-06-09 reorganizar informacion
    Updated the README to clarify assembly instructions and added a section for component functionality checks.
2026-06-09 Borrar el autotune
2026-06-09 Breve descripción de cada método y sus nombres en español
2026-06-09 Eliminé el _limitar
2026-06-09 detalles software
    Added details about software implementation and PID control.
2026-06-09 Cambio Variables PID
2026-06-10 Detalles PID y multimedia
    Updated assembly steps and PID tuning instructions in README.
2026-06-11 Deadband y angulo de caida
